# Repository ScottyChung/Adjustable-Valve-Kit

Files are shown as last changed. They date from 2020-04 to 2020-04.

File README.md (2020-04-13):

# Adjustable-Valve-Kit
Prototype kit for rapidly creating an adjustable valve using 3D printer and common components. 
This is a preliminary design that has not been thoroughly tested yet. It is not sealed from room air and may pull outside air in and leak air out.

Time to Build Estimate  
Print Time ~1.2Hrs  
Assembly ~0.5Hrs 

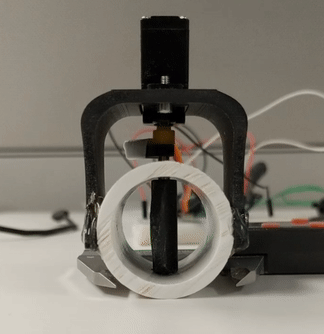
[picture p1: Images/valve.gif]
Valve

# Components
Components
* Servo Mounting Bracket
* Servo (HD-1800 is used and the bracket was designed with this servo in mind)
* Valve
* Rod Mount
* Stock Rod Material cut to 5-10mm longer than OD of PVC. See step 2 images. (Brass)
* PVC Pipe ~5inch length (Designed for 1" Sch 40)

# Assembly Instructions
1. Drill centered hole for rod to fit. Should be loose fit for rod to easily turn. If possible, have drill depth to indent the far side of the tube.
Drilling
Depth

2. Slide valve into pvc pipe and start to insert the rod. Sanding or filing a bevel on the rod is recommended to help starting the press fit. Using light taps from a hammer or a bench vise press the rod fully through the valve into the indention on the PVC pipe.
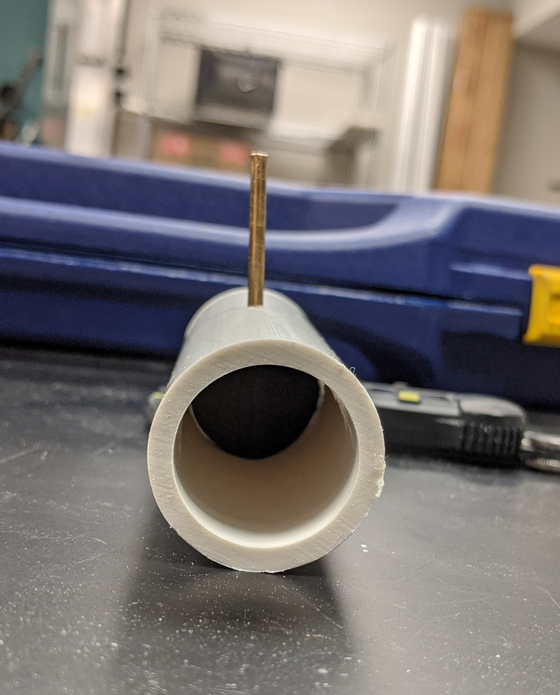
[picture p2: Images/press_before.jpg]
BeforePress

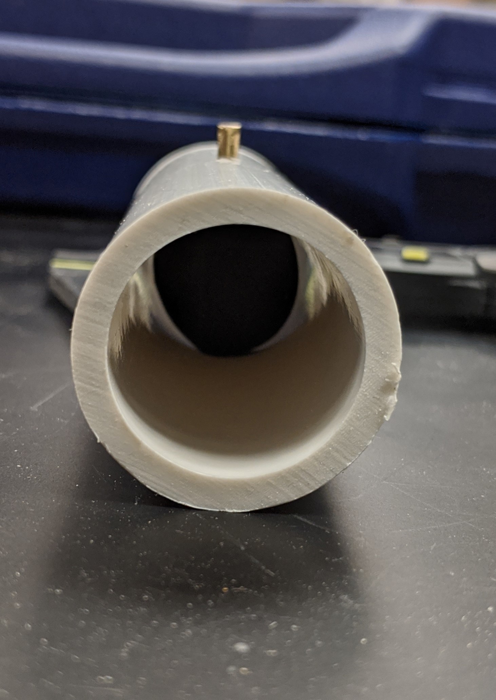
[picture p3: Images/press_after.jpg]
AfterPress


3. Test that the valve opens and closely freely, but is mated with the rod. Set the valve to the open position and press fit the rod mount piece so that it points parallel to the pipe. 
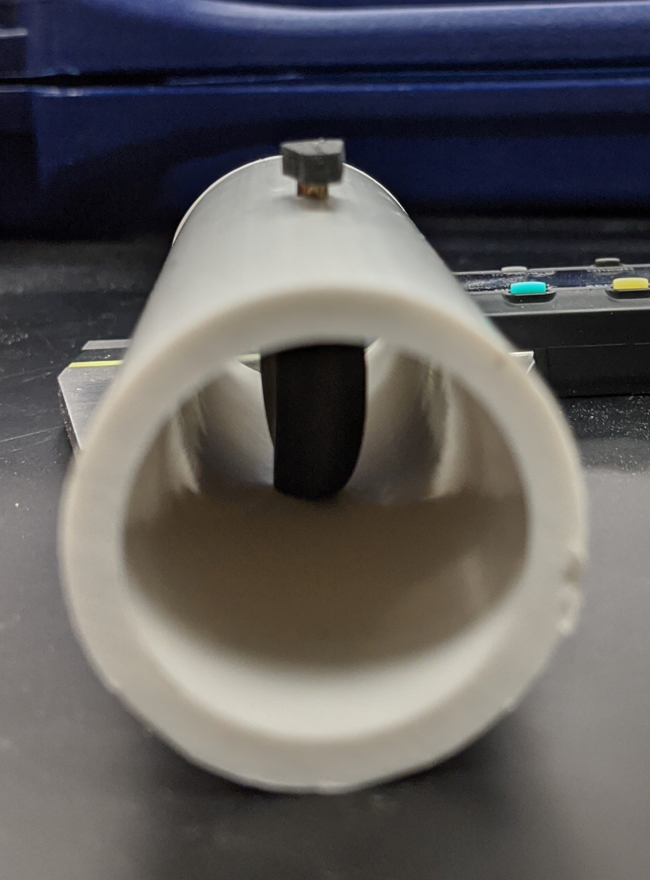
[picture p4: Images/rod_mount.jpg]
RodMount


4. Mount the servo to the bracket using two screws. Note the servo flanges are on top of the bracket not under.
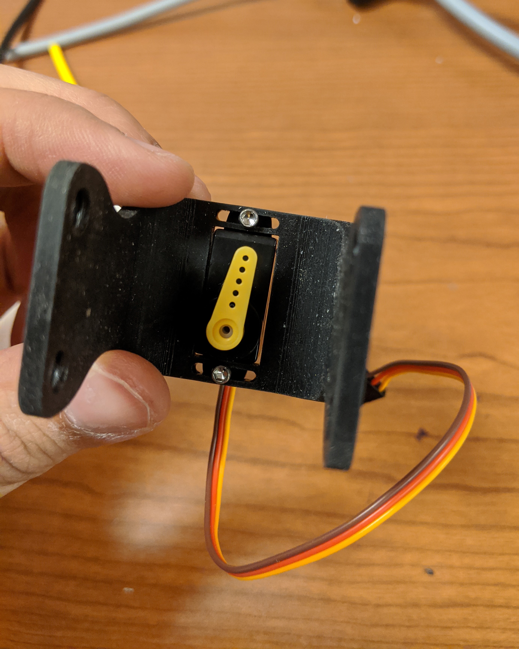
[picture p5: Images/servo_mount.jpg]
ServoMount


5. Ensure the servo is at a center location so that it has room to rotate in either direction. Match up the servo horn and rod mount. Attach the bracket to the PVC pipe using whatever method is available. The current set screw holes do not work very well so hot glue/ super glue works. Mate the servo horn and rod mount using a flexible material to help account for some of the misalignment. Currently, we are using heatshrink.
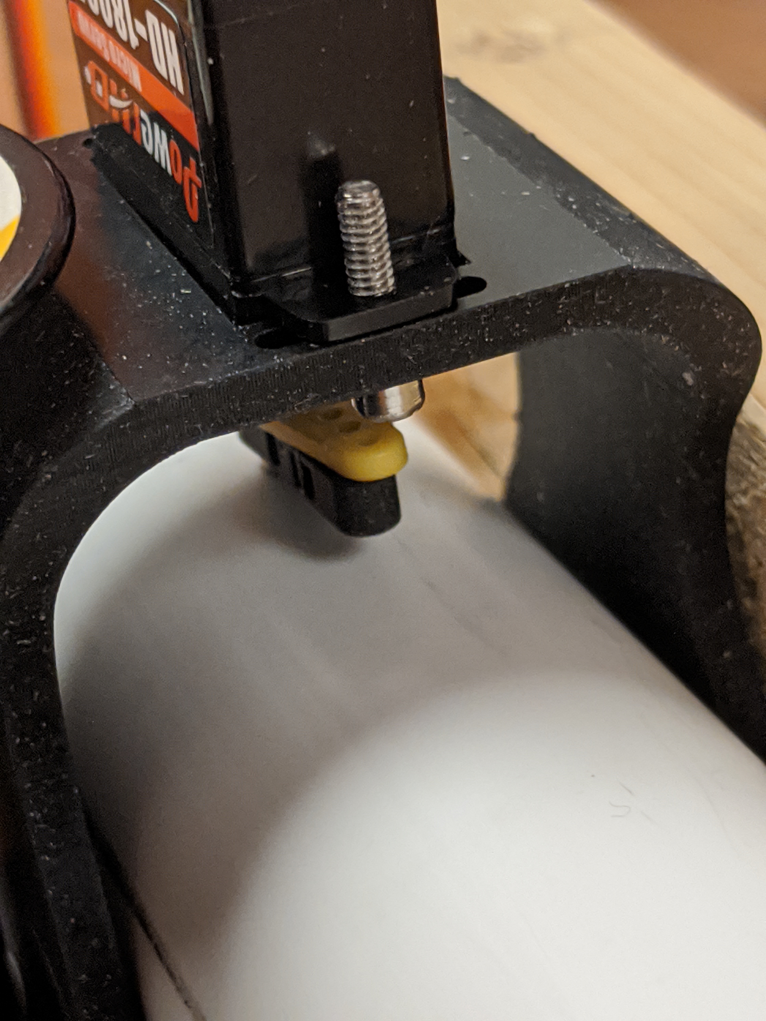
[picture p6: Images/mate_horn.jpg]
MateHorn


6. Now calibrate the fully open and close position of the valve. The open position is when the valve is as flat as possible obstruction the flow the least amount. Close position is when the valve is blocking as much as possible. **Ensure that the servo can reach the closed position without any humming or noise. Otherwise this could burnout the servo** Easiest method is to hook up a potentiometer to control the valve position, eyeball the fully open and closed position of valve, and record what values these are set at.
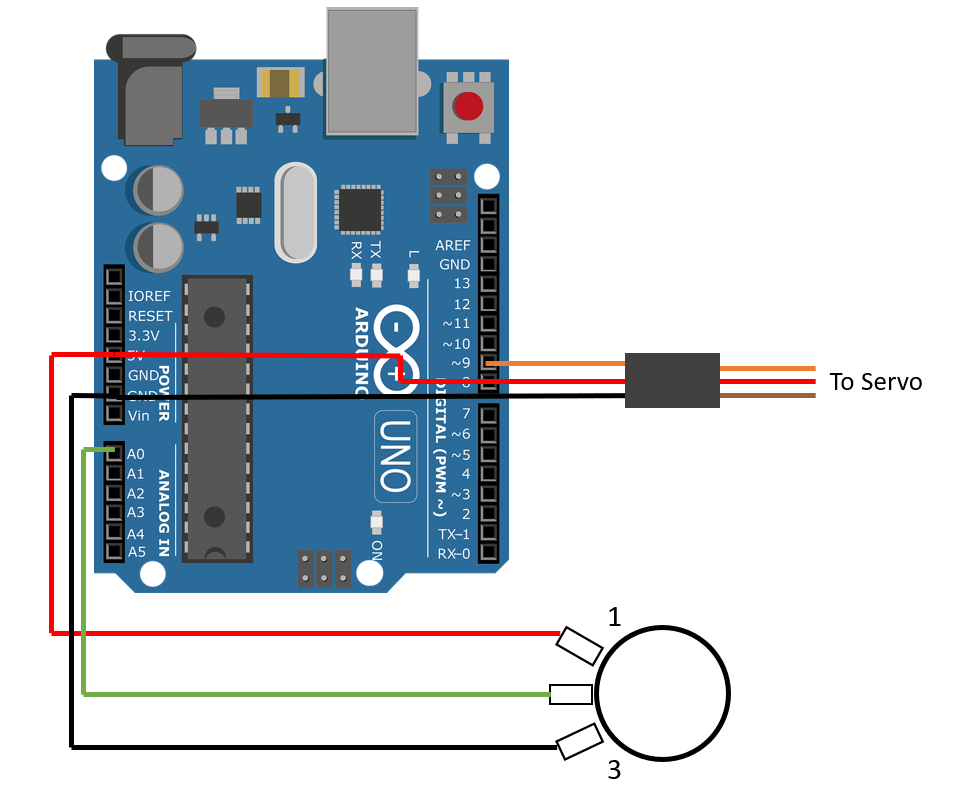
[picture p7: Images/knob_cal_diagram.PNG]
CalibDiagram

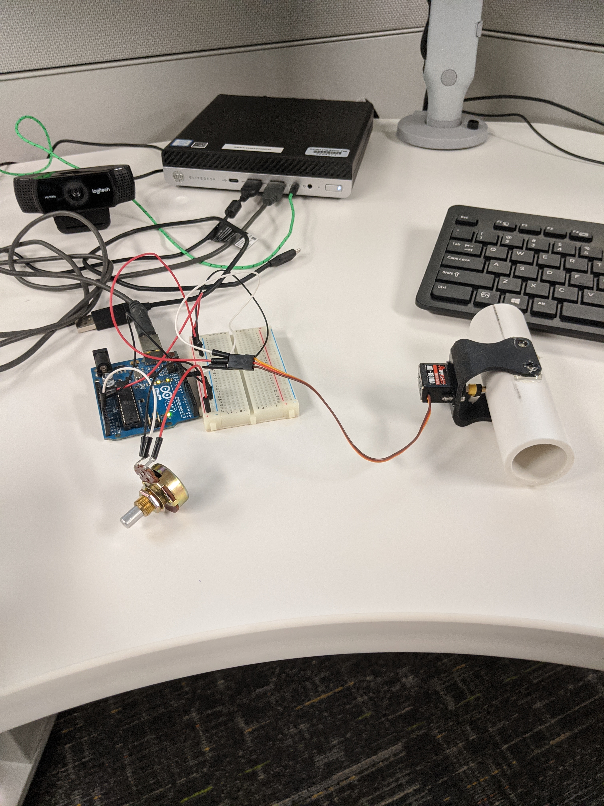
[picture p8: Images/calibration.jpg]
Calibration


# Todo
* Adding Build Instructions
* Improve Mounting option (Currently just use superglue)
* Have sealed version to avoid exposure to room air
* Endurance testing of part

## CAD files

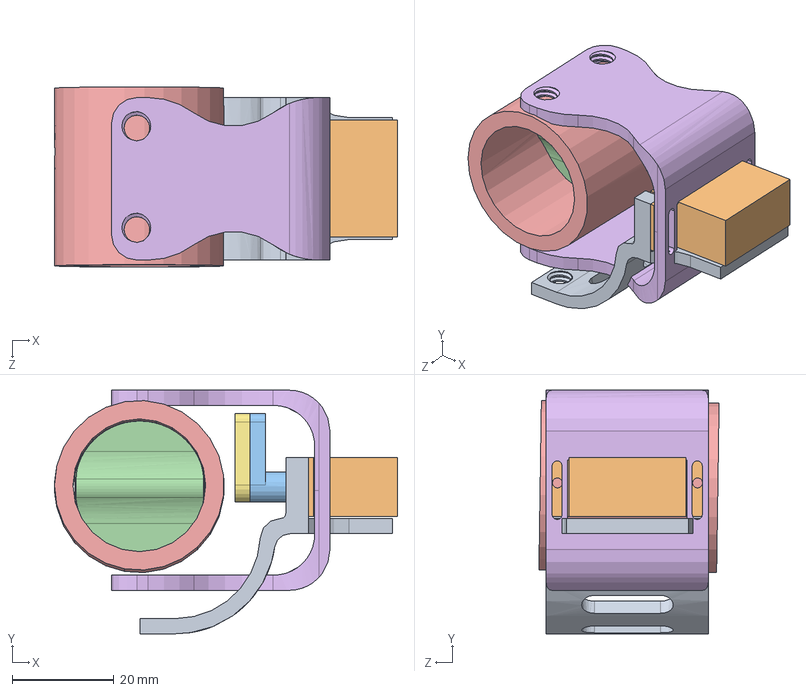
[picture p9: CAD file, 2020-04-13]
CAD/Adjustable Valve.SLDASM
67.5 x 48.0 x 35.5 mm
Servo Motor
Servo Horn^Adjustable Valve
Valve
PVC_1in_Sch40
Mount_Bracket
Rod Mount

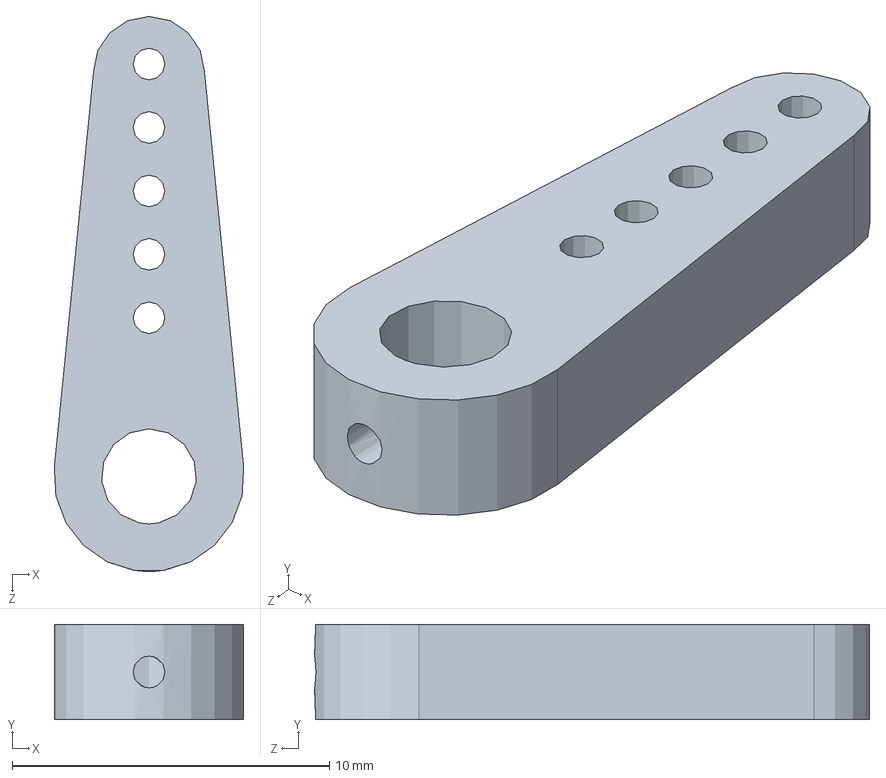
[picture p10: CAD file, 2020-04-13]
CAD/Rod Mount.SLDPRT
5.97 x 3.00 x 17.5 mm

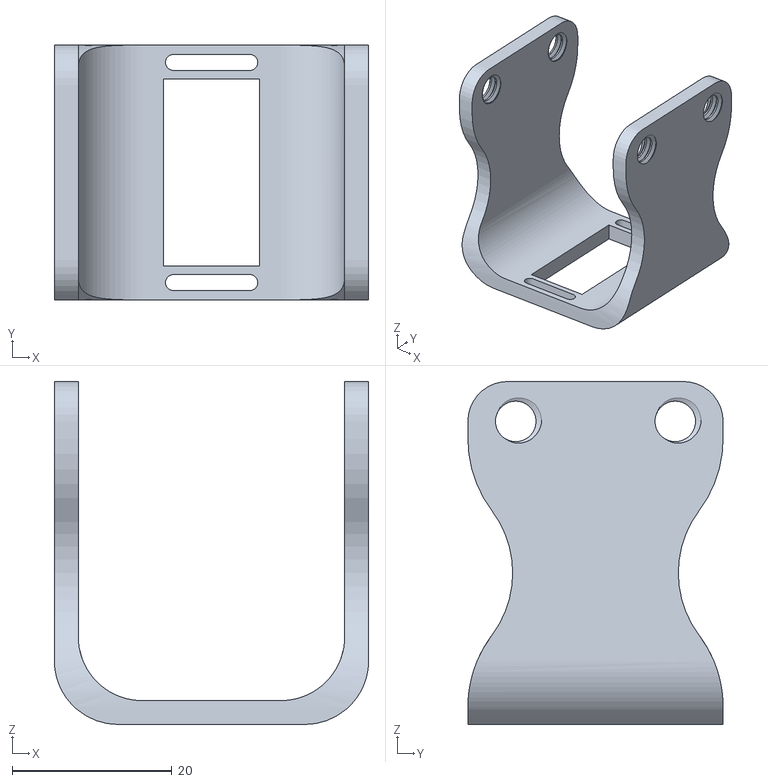
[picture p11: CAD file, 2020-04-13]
CAD/STLs/Mount_Bracket_V1.1.STL
39.4 x 32.0 x 43.0

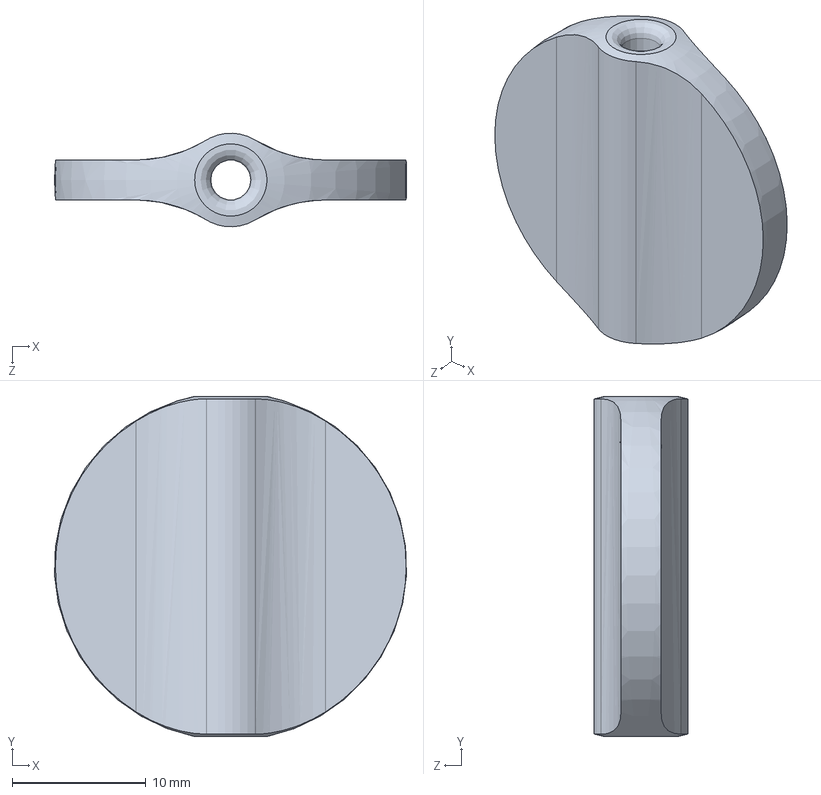
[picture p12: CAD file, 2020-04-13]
CAD/Valve.SLDPRT
26.3 x 25.4 x 6.99 mm

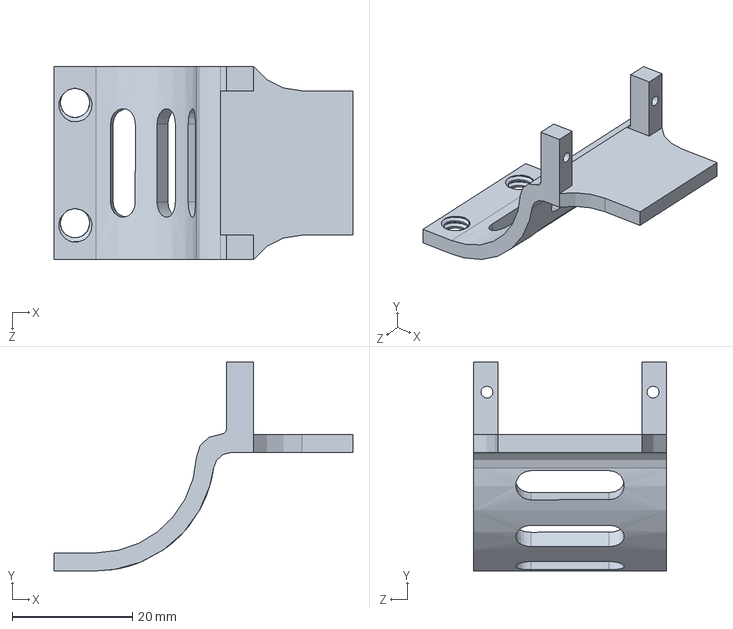
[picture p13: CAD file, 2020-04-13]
CAD/Bottom_Plate.SLDPRT
49.7 x 34.7 x 32.0 mm

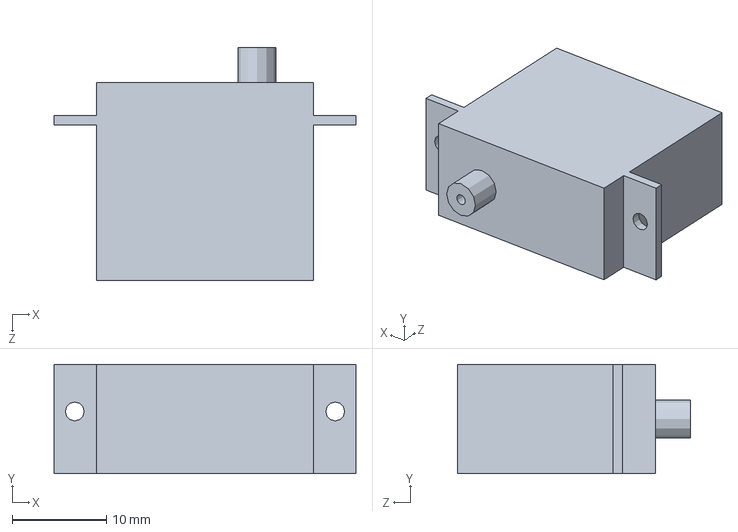
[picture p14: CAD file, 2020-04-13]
CAD/Servo Motor.SLDPRT
32.0 x 11.6 x 24.7 mm

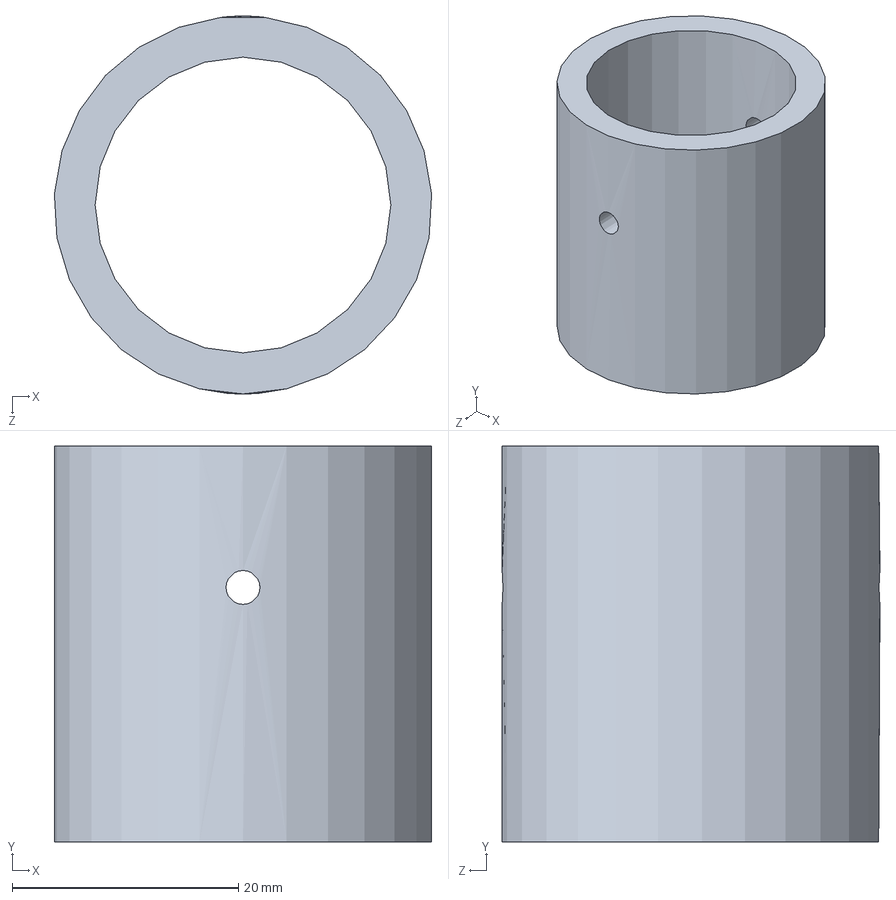
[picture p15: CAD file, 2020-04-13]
CAD/PVC_1in_Sch40.SLDPRT
33.3 x 35.0 x 33.4 mm

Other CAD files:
CAD/STLs/Rod Mount_V1.STL
CAD/Mount_Bracket.SLDPRT
CAD/STLs/Valve_V2.STL

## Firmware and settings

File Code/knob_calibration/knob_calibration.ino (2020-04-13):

/*
  knob_calibration

  Reads an analog input on pin 0, converts it to a servo range, sets a servo on pin 9 to the position, 
  and prints value to serial monitor.
*/
#include <Servo.h>

Servo myservo;

int servo_high = 180;
int servo_low = 0;
int pot_high = 1023;
int pot_low = 0;

// the setup routine runs once when you press reset:
void setup() {
  myservo.attach(9);
  // initialize serial communication at 9600 bits per second:
  Serial.begin(9600);
}

// the loop routine runs over and over again forever:
void loop() {
  // read the input on analog pin 0:
  int sensorValue = analogRead(A0);
  // Convert the analog reading (which goes from 0 - 1023) to a servo output (0,180):
  int servo_out = sensorValue * (float)(servo_high-servo_low)/(float)(pot_high-pot_low);
  // print out the servo values
  Serial.println(servo_out);
  // Write to servo
  myservo.write(servo_out);
}

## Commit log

2020-04-13 Adding cad files
    [Adjustable Valve.SLDASM, Bottom_Plate.SLDPRT, Mount_Bracket.SLDPRT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]
2020-04-13 moved cad into folder
    [Adjustable Valve.SLDASM, Bottom_Plate.SLDPRT, Mount_Bracket.SLDPRT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]
2020-04-13 added knob calib code and wiring diagram
2020-04-13 Correct diagram wiring
2020-04-13 added gif of valve
